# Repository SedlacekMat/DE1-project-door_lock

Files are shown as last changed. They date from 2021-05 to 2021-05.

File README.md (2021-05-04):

# Door lock with a four-digit PIN, twelve button keypad, a relay and the ability to change the PIN

### Team members

Sedláček David   
Sedláček Marek   
Sedláček Matyáš    
Sladkowski David     

[Github project folder]( https://github.com/SedlacekMat/DE1-project-door_lock)

### Project objectives

Create a door lock system with a PIN (4-digit) terminal, 12 push buttons, 4-digit 7-segment display and a relay for door lock control, with the ability to change the PIN after inputting the correct value. After not getting an input for a time, the device will reset itself.

Therefore we need to be able to: 
1. assign values to button presses, keep track of the position of the currently pressed digit
2. keep time for the autoreset after an idle period and for how long should the relay stay opened
3. store the value of the correct password in a way that enables changing it
4. compare the current value with the correct value for the current digit and eventually determine if the PIN is correct or not
5. drive a common anode 4-digit 7-segment display to show what has been pressed
6. make an external circuit for the buttons, relay, LEDs and display
7. make it work on Arty A7-35T/100T

## Hardware description
### ARTY A7-100

This project is based around the FPGA board ARTY A7-100T (has better capabilites when it comes to processing compared the ARTY A7-35T, therefore being better for potential future expansions, although if budget is a concern, the current version should run on the 35T as well with no problems). It is powered by 5V, the clock frequency is 100 MHz and has 256MB of RAM (DDR3L). Out of the available pins we have used the PMOD ones, which are grouped in four connectors of twelve pins (8 signal pins, 2 VCC, and 2 ground pins). Two of these connectors are high-speed, the other two are categorized as standard. The high-speed ones were used for the displays and the standard ones for buttons and such.

### External circuit

#### Schematic

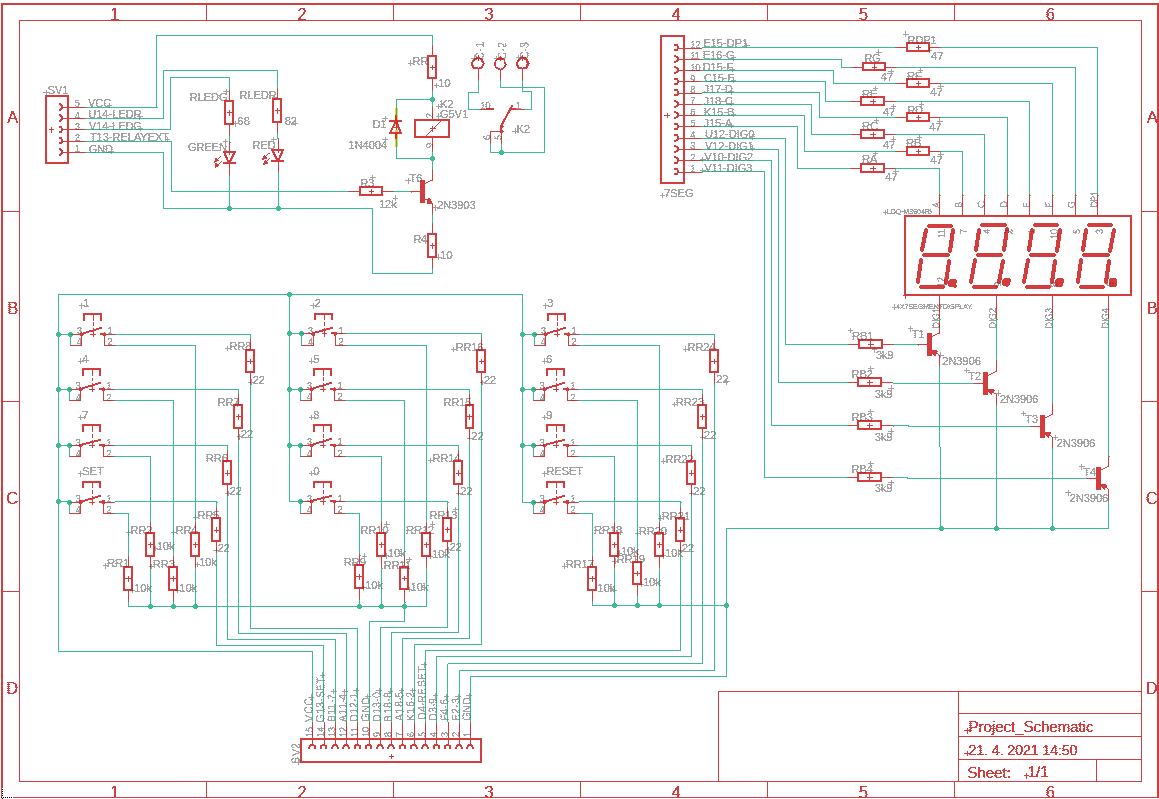
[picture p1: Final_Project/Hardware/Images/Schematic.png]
schematic


#### Used parts

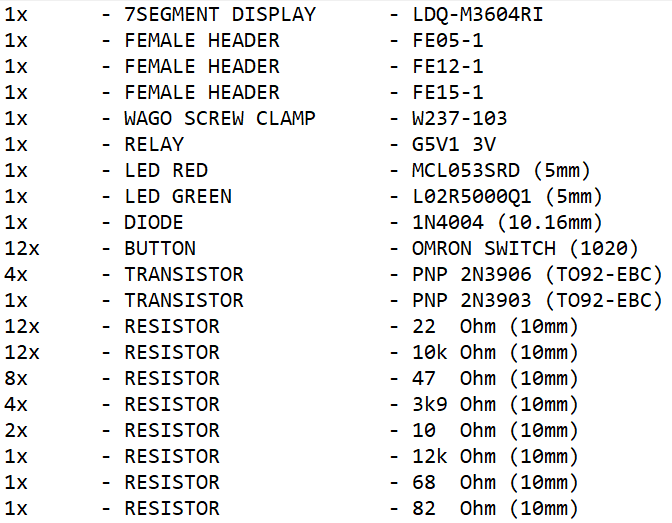
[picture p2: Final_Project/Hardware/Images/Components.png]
parts


#### Description

The external circuitry can be separated into three parts - the buttons, the display and the relay grouped with LEDs. 

The buttons have 3.3 V on their input, when a button is pressed, the voltage is transfered to the FPGA board input. They're connected to the supply voltage through 10k ohm resistors, this ensures that at the input of ARTY A7-100T, we can only get either a logical 1 or a logical 0, preventing undeterminable states. The 22 ohm resistors serve as protection. Each button has its own pin connection, due to the number of pins on the board being high enough for the projects needs. Potential improvement to save more pins (if the project were to be expanded input/output-wise) would be to connect them in a matrix.

For the display, the signals come in through 47 ohm resistors connected to the cathodes of the individual segments. The display used is the common anode type. The four PNP transistors are there to ensure only one display can be lit up at the same time. The anodes will be switching at periodic intervals, too fast for human vision, thus appearing as if all the diplays are lit at the same time.

As for the LEDs and the relay, the current through the red LED is limited by an 82 ohm resistor, 68 ohm for the green one. These prevent them from burning. The red LED will light up, if the PIN is incorrect, the green one in the opposite case. The relay is controlled by an NPN transistor, which, after it's base goes high, will open the relay. Connected parallel to the relay is a diode, through which the relay coil can discharge, after the relay is turned off.

Below are images of the PCB design

### PCB design

#### PCB top

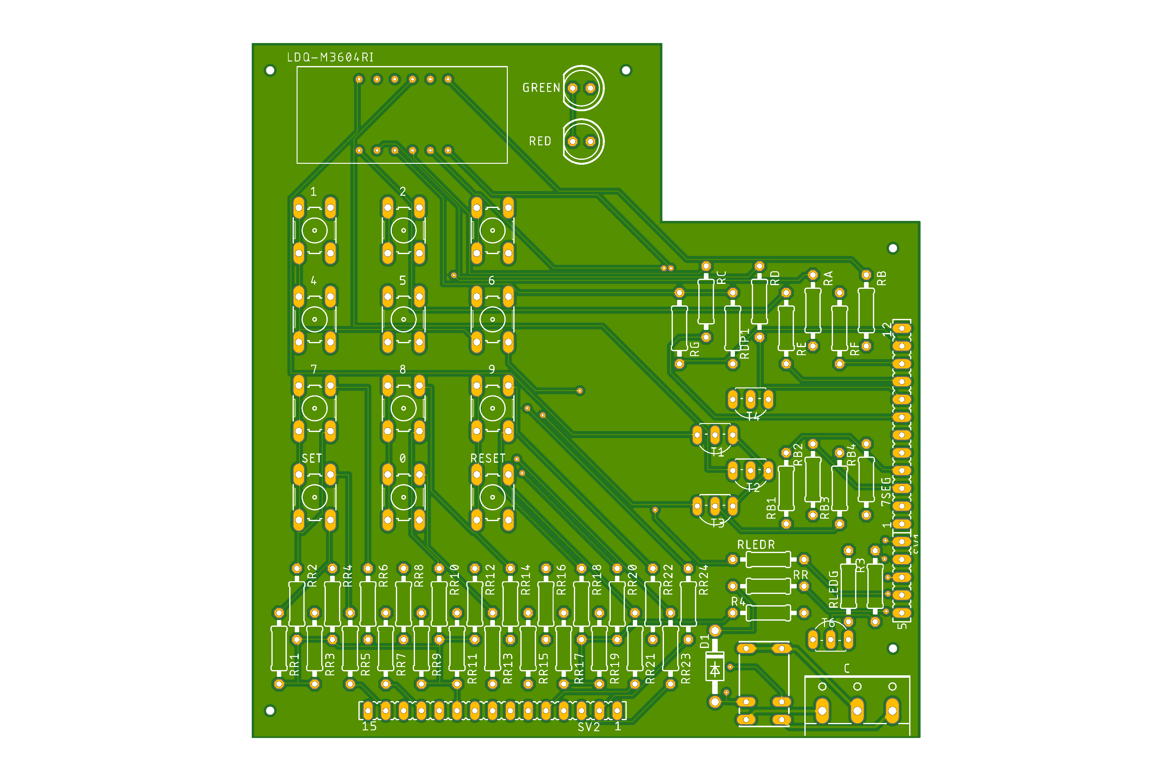
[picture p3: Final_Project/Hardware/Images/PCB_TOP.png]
PCBtop


#### PCB bottom

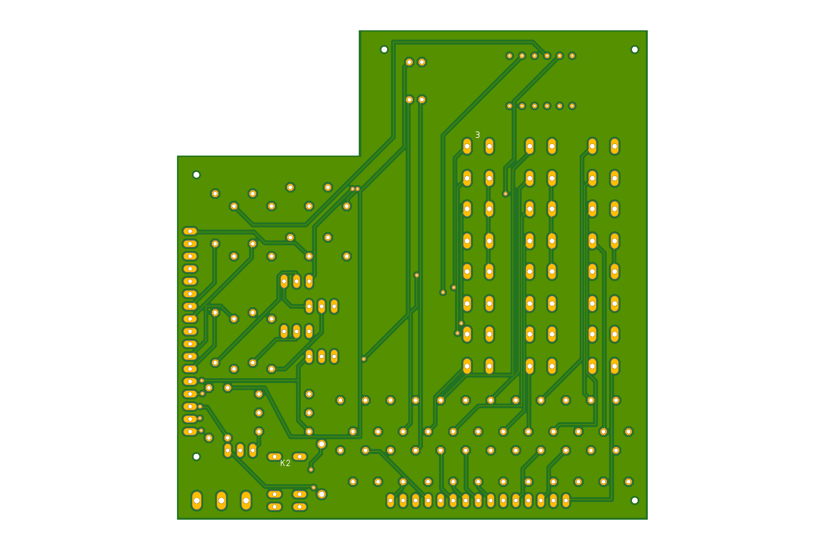
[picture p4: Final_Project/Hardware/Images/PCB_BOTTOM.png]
PCBbottom


#### PCB 3D model

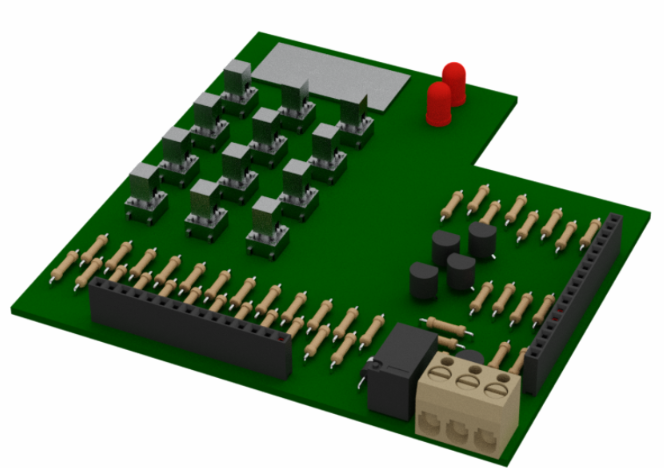
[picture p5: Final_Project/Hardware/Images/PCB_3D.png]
PCB3D


## VHDL modules description and simulations

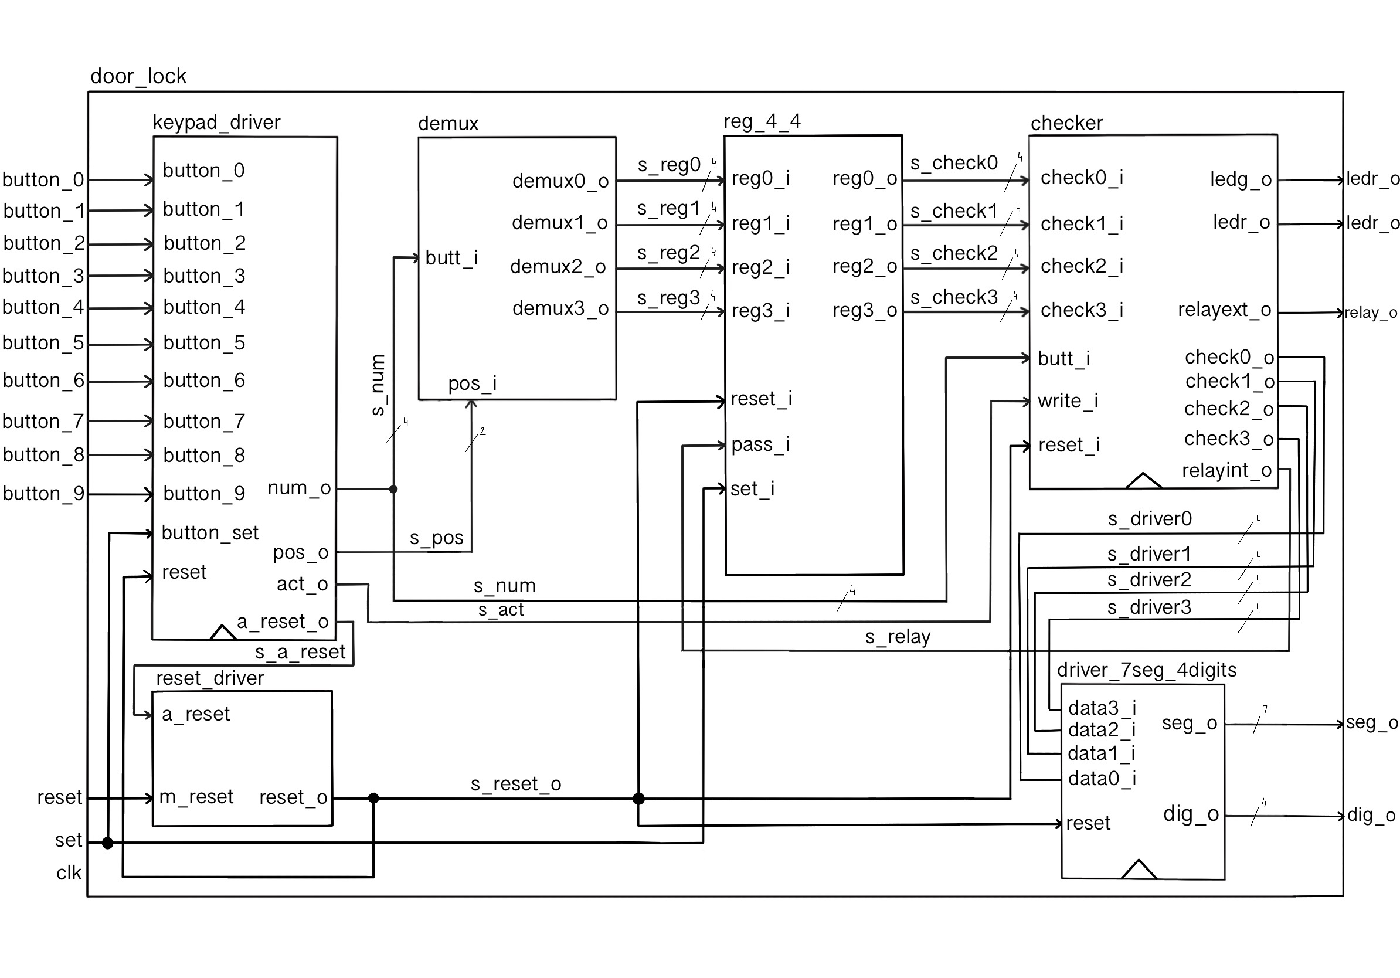
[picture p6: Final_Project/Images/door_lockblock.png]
doorlockblock


### keypad_driver

#### Visual representation:

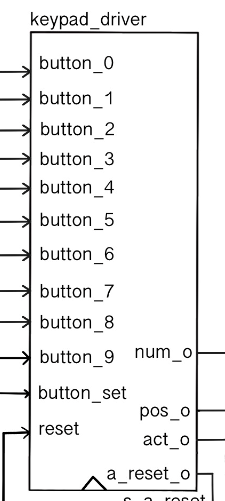
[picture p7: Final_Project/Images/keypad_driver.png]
keypaddriverblock


#### State diagram:

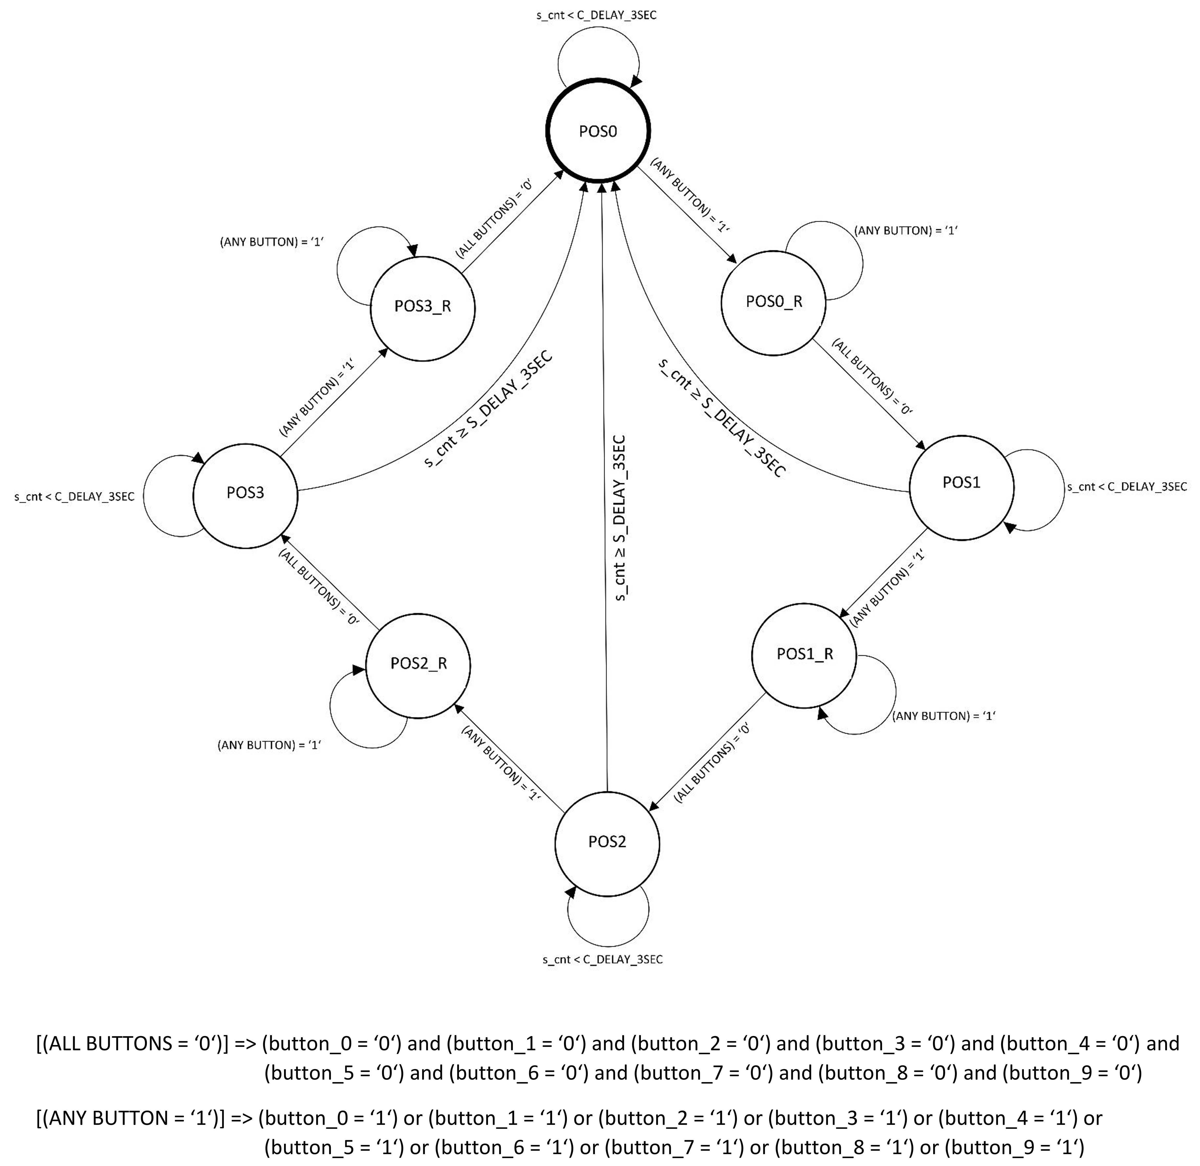
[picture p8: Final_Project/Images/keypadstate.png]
keypaddriverstate


#### Description:

The keypad_driver block functions as a middleman, first translating information from the input buttons and then transferring it to the checker block. A decision was made early in the project development to discard the idea of a button matrix input in favor of working with individual buttons, seeing as the FPGA board used has enough input/output pins to do so. This also determined parts of the design of the external board, which was shown and discussed above.

The keypad_driver provides the rest of the blocks with information about keypresses, assigns 4-bit values to buttons and keeps track of the position at which the value should appear. It uses a finite state machine to cycle through 4 positions using 8 states. The reason it uses 2 states (wait for press and wait for release) for each position, is to precisely determine whether the pressed button has been released, so it can without any doubt jump to the next position. While no button is pressed, the keypad-driver sends out a 4-bit signal of “1111”, indicating to the other blocks that there is no input.

Keypad_driver also handles the automatic reset function which activates after an idle period with no input. This function has been implemented so that the lock wipes itself in the case that someone inputs, for example, two values and walks off.

From the simulation waveforms, we see that the outputted position starts correctly indexing from 0, and (although we can't see here if they are actually correct, will be seen in the other simulations) button presses change the button value output's value. We can see that two buttons at the same time are sent out as only a single number out of the two (we can count button presses by s_act, only when it's '1' is the button press legitimate), which is important for the correct function of the rest of the blocks. We also see the autoreset turning on after an idle period with no button presses, here it's arbitrary, for the simulation to be fast, the time can be changed by changing the c_DELAY_1SEC to a more realistic value.

#### Simulation waveforms:

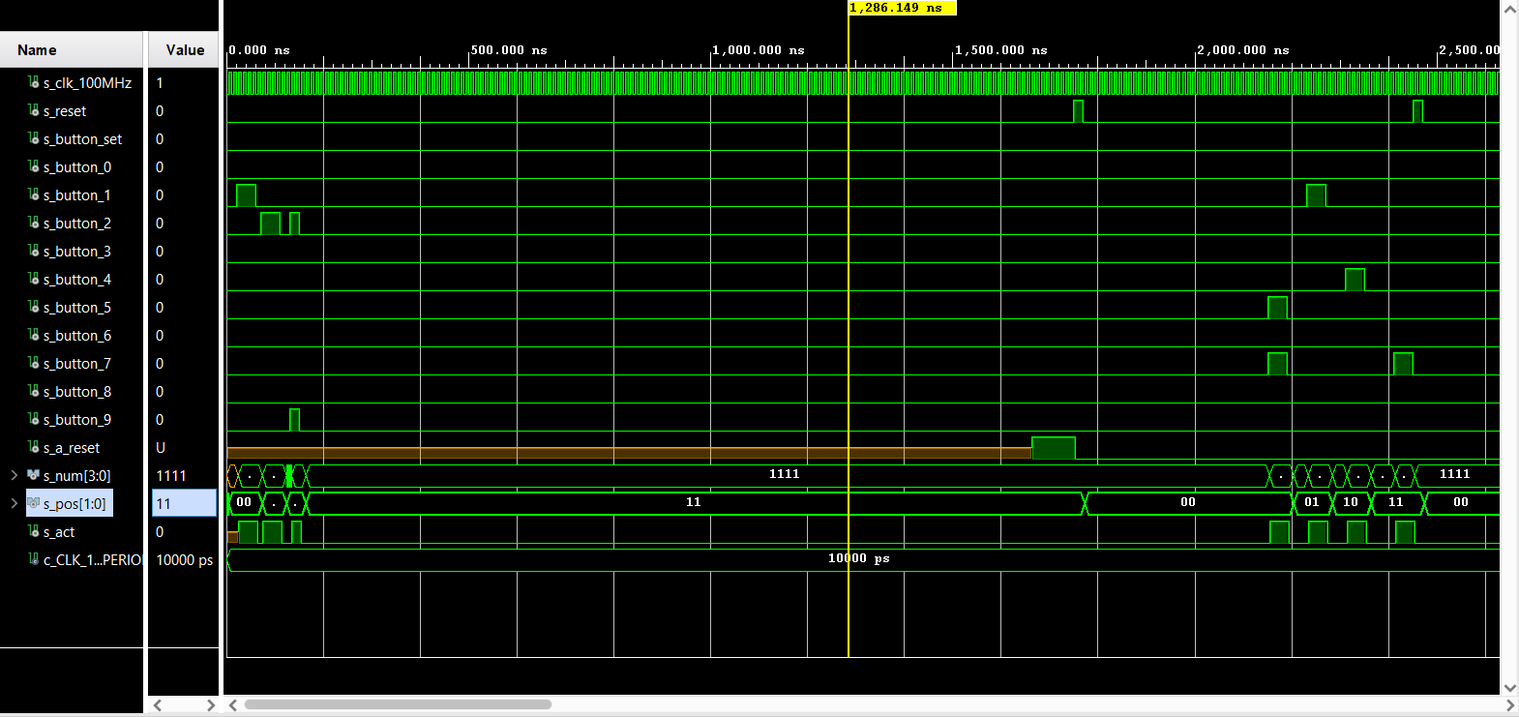
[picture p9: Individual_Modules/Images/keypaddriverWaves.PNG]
keypaddriverWaves


#### testbench: [tb_keypad_driver.vhd](Individual_Modules/Testbenches/tb_keypad_driver.vhd)

#### VHDL architecture:
```vhdl
architecture Behavioral of keypad_driver is

    type decoder_state is (POS0, POS0_R, POS1, POS1_R, POS2, POS2_R, POS3, POS3_R);
    signal s_state  : decoder_state;

    signal s_cnt    : unsigned(8 - 1 downto 0);

    constant c_DELAY_1SEC : unsigned(8 - 1 downto 0) := b"1001_0110";
    constant c_ZERO       : unsigned(8 - 1 downto 0) := b"0000_0000";
    
begin
    p_decoder_fsm : process(clk)
    begin
        if rising_edge(clk) then
            if (reset = '1') then
                s_state <= POS0;
                
                num_o   <= "1111";
                act_o   <= '0';
                -- Reset counter
                s_cnt   <= c_ZERO;
                
                a_reset_o <= '0';
           
            else
                case s_state is
                
                    when POS0 =>
                        
                        pos_o <= "00";
                        
                        if (button_0 = '1') then                          
                            num_o   <= "0000";
                            s_state <= POS0_R;
                            act_o <= '1';
                            s_cnt <= c_ZERO;
                        elsif (button_1 = '1') then   
                            num_o <= "0001";
                            s_state <= POS0_R;
                            act_o <= '1';
                            s_cnt <= c_ZERO;
                        elsif (button_2 = '1') then   
                            num_o <= "0010";
                            s_state <= POS0_R;
                            act_o <= '1';
                            s_cnt <= c_ZERO;
                        elsif (button_3 = '1') then   
                            num_o <= "0011";
                            s_state <= POS0_R;
                            act_o <= '1';
                            s_cnt <= c_ZERO;    
                        elsif (button_4 = '1') then   
                            num_o <= "0100";
                            s_state <= POS0_R;
                            act_o <= '1';
                            s_cnt <= c_ZERO;        
                        elsif (button_5 = '1') then   
                            num_o <= "0101";
                            s_state <= POS0_R;
                            act_o <= '1';
                            s_cnt <= c_ZERO;       
                        elsif (button_6 = '1') then   
                            num_o <= "0110";
                            s_state <= POS0_R;
                            act_o <= '1';
                            s_cnt <= c_ZERO;         
                        elsif (button_7 = '1') then   
                            num_o <= "0111";
                            s_state <= POS0_R;
                            act_o <= '1';
                            s_cnt <= c_ZERO;         
                        elsif (button_8 = '1') then   
                            num_o <= "1000";
                            s_state <= POS0_R;
                            act_o <= '1';
                            s_cnt <= c_ZERO;         
                        elsif (button_9 = '1') then   
                            num_o <= "1001";
                            s_state <= POS0_R;
                            act_o <= '1';
                            s_cnt <= c_ZERO;         
                        --else
                 
                        end if;
                        
                    when POS0_R =>
                        
                        pos_o <= "00";
                        
                        if (button_0 = '0' and button_1 = '0' and
                            button_2 = '0' and button_3 = '0' and
                            button_4 = '0' and button_5 = '0' and
                            button_6 = '0' and button_7 = '0' and
                            button_8 = '0' and button_9 = '0') then
                            s_state <= POS1;
                            act_o <= '0';     
                        end if;
                        
                    when POS1 =>
                        
                        pos_o <= "01";
                        
                        if (button_0 = '1') then                          
                            num_o   <= "0000";
                            s_state <= POS1_R;
                            act_o <= '1';
                            s_cnt <= c_ZERO;
                        elsif (button_1 = '1') then   
                            num_o <= "0001";
                            s_state <= POS1_R;
                            act_o <= '1';
                            s_cnt <= c_ZERO;   
                        elsif (button_2 = '1') then   
                            num_o <= "0010";
                            s_state <= POS1_R;
                            act_o <= '1';
                            s_cnt <= c_ZERO;        
                        elsif (button_3 = '1') then   
                            num_o <= "0011";
                            s_state <= POS1_R;
                            act_o <= '1';
                            s_cnt <= c_ZERO;
                        elsif (button_4 = '1') then   
                            num_o <= "0100";
                            s_state <= POS1_R;
                            act_o <= '1';
                            s_cnt <= c_ZERO;       
                        elsif (button_5 = '1') then   
                            num_o <= "0101";
                            s_state <= POS1_R;
                            act_o <= '1';
                            s_cnt <= c_ZERO;          
                        elsif (button_6 = '1') then   
                            num_o <= "0110";
                            s_state <= POS1_R;
                            act_o <= '1';
                            s_cnt <= c_ZERO;          
                        elsif (button_7 = '1') then   
                            num_o <= "0111";
                            s_state <= POS1_R;
                            act_o <= '1';
                            s_cnt <= c_ZERO;  
                        elsif (button_8 = '1') then   
                            num_o <= "1000";
                            s_state <= POS1_R;
                            act_o <= '1';
                            s_cnt <= c_ZERO;       
                        elsif (button_9 = '1') then   
                            num_o <= "1001";
                            s_state <= POS1_R;
                            act_o <= '1';
                            s_cnt <= c_ZERO;        
                        else
                            if (s_cnt < c_DELAY_1SEC) then
                                s_cnt <= s_cnt + 1;
                                num_o <= "1111";
                            else
                                -- s_state <= POS0;
                                -- s_cnt <= c_ZERO;
                                a_reset_o <= '1';
                            end if;  
                        end if;
                        
                    when POS1_R =>
                        
                        pos_o <= "01";
                        
                        if (button_0 = '0' and button_1 = '0' and
                            button_2 = '0' and button_3 = '0' and
                            button_4 = '0' and button_5 = '0' and
                            button_6 = '0' and button_7 = '0' and
                            button_8 = '0' and button_9 = '0') then
                            s_state <= POS2;
                            act_o <= '0';                        
                        end if; 
                       
                    when POS2 =>
                        
                        pos_o <= "10";
                        
                        if (button_0 = '1') then                          
                            num_o   <= "0000";
                            s_state <= POS2_R;
                            act_o <= '1';
                            s_cnt <= c_ZERO;
                        elsif (button_1 = '1') then   
                            num_o <= "0001";
                            s_state <= POS2_R;
                            act_o <= '1';
                            s_cnt <= c_ZERO; 
                        elsif (button_2 = '1') then   
                            num_o <= "0010";
                            s_state <= POS2_R;
                            act_o <= '1';
                            s_cnt <= c_ZERO;      
                        elsif (button_3 = '1') then   
                            num_o <= "0011";
                            s_state <= POS2_R;
                            act_o <= '1';
                            s_cnt <= c_ZERO;         
                        elsif (button_4 = '1') then   
                            num_o <= "0100";
                            s_state <= POS2_R;
                            act_o <= '1';
                            s_cnt <= c_ZERO;        
                        elsif (button_5 = '1') then   
                            num_o <= "0101";
                            s_state <= POS2_R;
                            act_o <= '1';
                            s_cnt <= c_ZERO;         
                        elsif (button_6 = '1') then   
                            num_o <= "0110";
                            s_state <= POS2_R;
                            act_o <= '1';
                            s_cnt <= c_ZERO;        
                        elsif (button_7 = '1') then   
                            num_o <= "0111";
                            s_state <= POS2_R;
                            act_o <= '1';
                            s_cnt <= c_ZERO;       
                        elsif (button_8 = '1') then   
                            num_o <= "1000";
                            s_state <= POS2_R;
                            act_o <= '1';
                            s_cnt <= c_ZERO;         
                        elsif (button_9 = '1') then   
                            num_o <= "1001";
                            s_state <= POS2_R;
                            act_o <= '1';
                            s_cnt <= c_ZERO;         
                        else
                            if (s_cnt < c_DELAY_1SEC) then
                                s_cnt <= s_cnt + 1;
                                num_o <= "1111";
                            else
                                -- s_state <= POS0;
                                -- s_cnt <= c_ZERO;
                                a_reset_o <= '1';
                            end if;                            
                        end if;
                        
                    when POS2_R =>
                        
                        pos_o <= "10";
                        
                        if (button_0 = '0' and button_1 = '0' and
                            button_2 = '0' and button_3 = '0' and
                            button_4 = '0' and button_5 = '0' and
                            button_6 = '0' and button_7 = '0' and
                            button_8 = '0' and button_9 = '0') then
                            s_state <= POS3;
                            act_o <= '0';                      
                        end if; 
                        
                    when POS3 =>
                        
                        pos_o <= "11";
                        
                        if (button_0 = '1') then                          
                            num_o   <= "0000";
                            s_state <= POS3_R;
                            act_o <= '1';
                            s_cnt <= c_ZERO;
                        elsif (button_1 = '1') then   
                            num_o <= "0001";
                            s_state <= POS3_R;
                            act_o <= '1';
                            s_cnt <= c_ZERO;    
                        elsif (button_2 = '1') then   
                            num_o <= "0010";
                            s_state <= POS3_R;
                            act_o <= '1';
                            s_cnt <= c_ZERO;         
                        elsif (button_3 = '1') then   
                            num_o <= "0011";
                            s_state <= POS3_R;
                            act_o <= '1';
                            s_cnt <= c_ZERO;         
                        elsif (button_4 = '1') then   
                            num_o <= "0100";
                            s_state <= POS3_R;
                            act_o <= '1';
                            s_cnt <= c_ZERO;        
                        elsif (button_5 = '1') then   
                            num_o <= "0101";
                            s_state <= POS3_R;
                            act_o <= '1';
                            s_cnt <= c_ZERO;        
                        elsif (button_6 = '1') then   
                            num_o <= "0110";
                            s_state <= POS3_R;
                            act_o <= '1';
                            s_cnt <= c_ZERO;        
                        elsif (button_7 = '1') then   
                            num_o <= "0111";
                            s_state <= POS3_R;
                            act_o <= '1';
                            s_cnt <= c_ZERO;       
                        elsif (button_8 = '1') then   
                            num_o <= "1000";
                            s_state <= POS3_R;
                            act_o <= '1';
                            s_cnt <= c_ZERO;         
                        elsif (button_9 = '1') then   
                            num_o <= "1001";
                            s_state <= POS3_R;
                            act_o <= '1';
                            s_cnt <= c_ZERO;
                        else
                            if (s_cnt < c_DELAY_1SEC) then
                                s_cnt <= s_cnt + 1;
                                num_o <= "1111";
                            else
                                -- s_state <= POS0;
                                -- s_cnt <= c_ZERO;
                                a_reset_o <= '1';
                            end if;
                        end if;
                        
                    when POS3_R =>
                        
                        pos_o <= "11";
                        
                        if (button_0 = '0' and button_1 = '0' and
                            button_2 = '0' and button_3 = '0' and
                            button_4 = '0' and button_5 = '0' and
                            button_6 = '0' and button_7 = '0' and
                            button_8 = '0' and button_9 = '0' and
                            button_set = '0') then
                            s_state <= POS0;
                            act_o <= '0';          
                        end if; 
                                   
                end case;
            end if; 
        end if;
    end process p_decoder_fsm; 

end Behavioral;
``` 

### reset_driver

#### Visual representation:

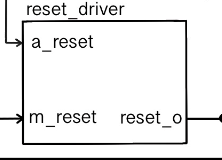
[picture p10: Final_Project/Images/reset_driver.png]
resetdriverblock


#### Description:

Reset driver is a simple block, working as an OR gate for 2 input signals. Both are one-bit signals, one sent form keypad_driver as an auto-reset, the other is connected to the reset button on the external board. After any of reset_driver’s inputs is set HIGH (equal to ‘1’) it drives the output signal HIGH as well, which in this case resets all the modules connected to the output. It has been created to enable the keypad_driver to reset the whole project.

#### Simulation waveforms:

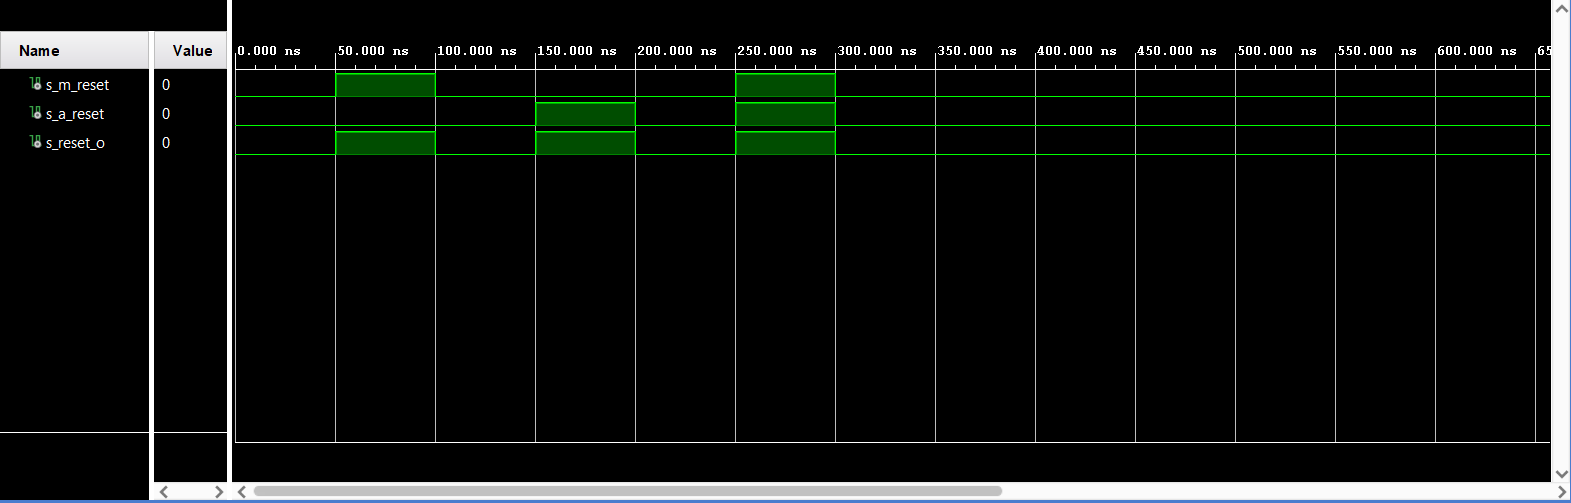
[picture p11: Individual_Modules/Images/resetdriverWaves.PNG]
resetdriverWaves


#### testbench: [tb_reset_driver.vhd](Individual_Modules/Testbenches/tb_reset_driver.vhd)

#### VHDL architecture:
```vhdl
architecture Behavioral of reset_driver is

begin
    p_reset_driver : process(m_reset, a_reset)
    begin
        
        if (a_reset = '1' or m_reset = '1') then
            reset_o <= '1';
        else
            reset_o <= '0';
        end if;
        
    end process p_reset_driver;

end Behavioral;
``` 

### demux

#### Visual representation:

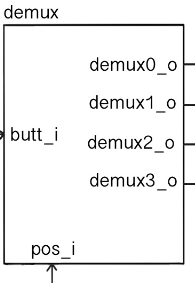
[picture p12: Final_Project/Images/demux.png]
demuxblock


#### Description:

This block is, as the name suggests, a demultiplexer. It's job is to assign the 4-bit button value input (butt_i) to one of the outputs based on the value of the 2-bit position input (pos_i). It's the first block of the two block system for the storage of the correct combination. It is always active, even when the PIN is not being changed, since there is no need to turn it off, that becomes important only on the second block of the password storage system, the 4 times 4-bit register.

In the simulation we see the behaviour exactly as described above, the input being assigned to an output based on the value of the position coming in from keypad_driver.

#### Simulation waveforms:

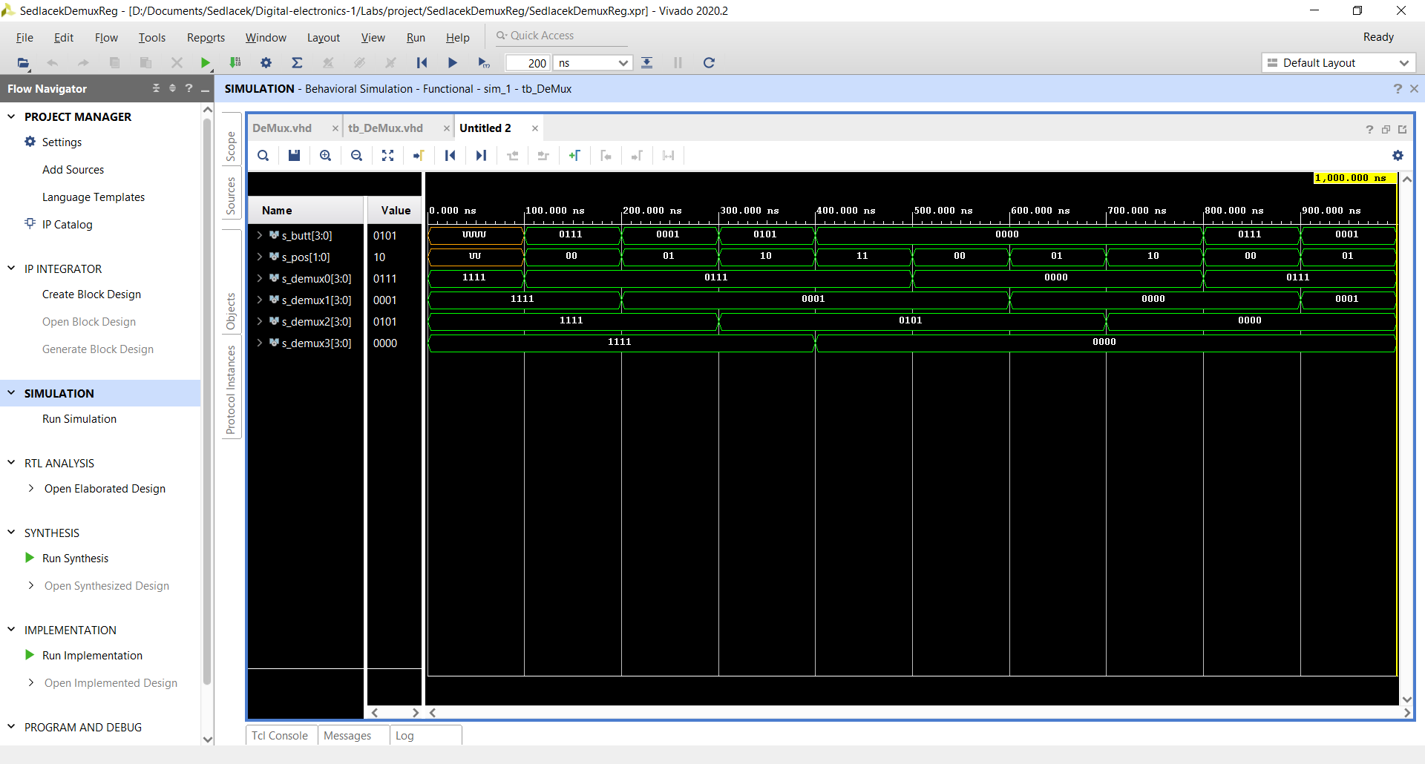
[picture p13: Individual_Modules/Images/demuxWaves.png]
demuxWaves


#### testbench: [tb_DeMux.vhd](Individual_Modules/Testbenches/tb_DeMux.vhd)

#### VHDL architecture:
```vhdl
architecture Behavioral of demux is
        begin
        
        p_demux : process(pos_i, butt_i)
        begin

            case pos_i is
                when "00" => 
                    demux0_o <= butt_i;
                when "01" => 
                    demux1_o <= butt_i;
                when "10" => 
                    demux2_o <= butt_i;
                when "11" => 
                    demux3_o <= butt_i;
                when others =>
                    demux0_o <= "1111";
                    demux1_o <= "1111";
                    demux2_o <= "1111";
                    demux3_o <= "1111";
             end case;      
        
        end process p_demux;
    end Behavioral;
``` 

### reg_4_4

#### Visual representation:

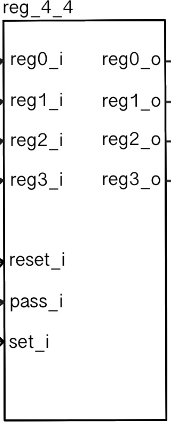
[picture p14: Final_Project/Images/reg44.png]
reg44block


#### Description:

This block is a 16-bit register, split into four 4-bit registers. In principle, it's basically a group of D latches with a condition on the enable input. It's job is to, if the set_i (activated by a button which must be held) and pass_i (which is active ONLY when the door is unlocked by entering the correct password, for a predetermined amount of time) inputs are set high, record and store the inputs coming from the demultiplexer into the correct outputs, thus changing the combination of values that the checker block (where the comparation of the current and correct values takes place) will read. In the situation that the set_i, pass_i and reset_i inputs are all activated, the correct PIN (register output) will change to the combination "3142". The local check signal is present so that the register isn't permanently stuck in the default password branch.

In the simulation waves, we see that just the pass_i has no effect. When combined with set_i, input values start getting assigned to their corresponding output. If only set is on, nothing changes, (same for reset, not shown here, but obvious from the final project waveforms). If pass,set and reset are on, we change to the default combination.

#### Simulation waveforms:

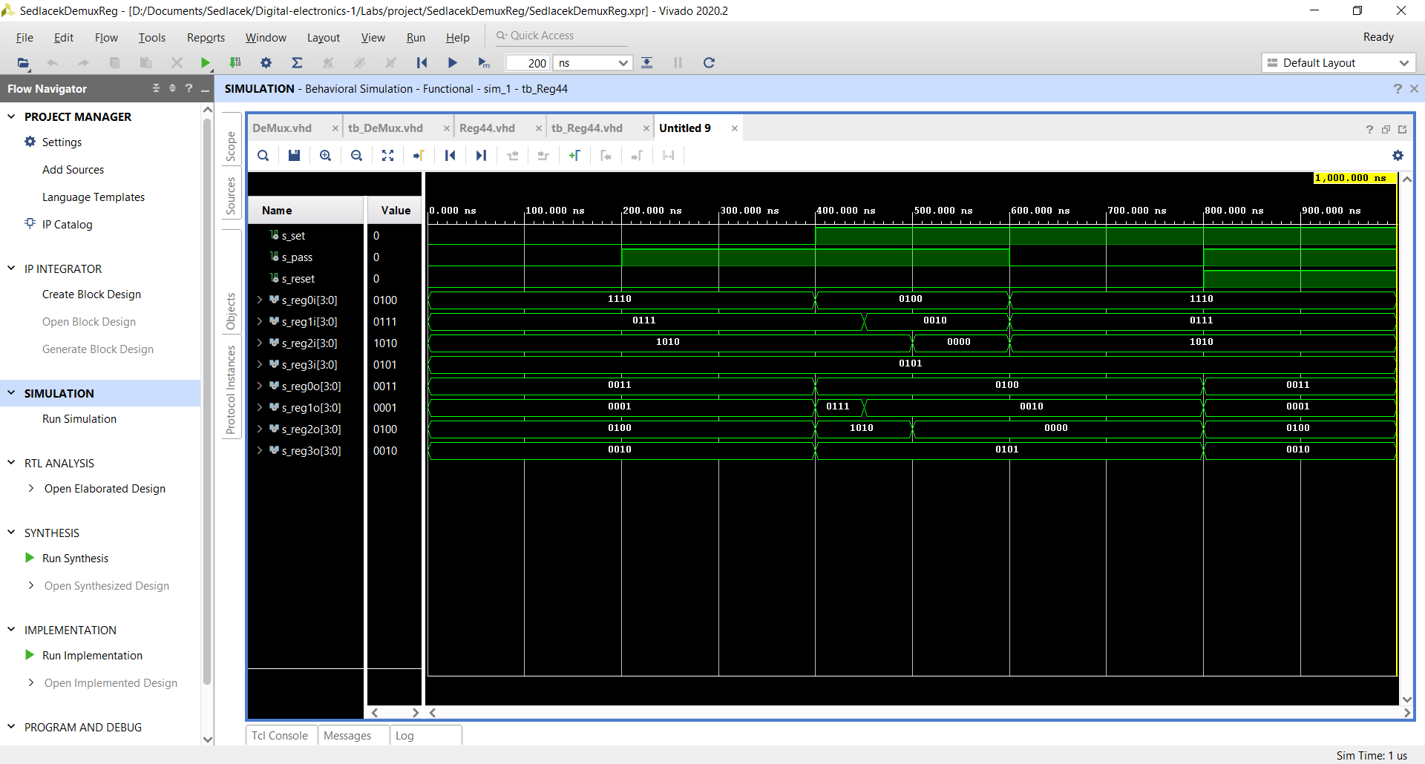
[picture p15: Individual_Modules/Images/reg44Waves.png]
reg44Waves


#### testbench: [tb_Reg44.vhd](Individual_Modules/Testbenches/tb_Reg44.vhd)

#### VHDL architecture:
```vhdl

architecture Behavioral of reg_4_4 is

    signal s_local_check : std_logic;

begin

    p_register : process(pass_i, set_i, reset_i, reg0_i, reg1_i, reg2_i, reg3_i)
    begin
    
    if (pass_i='1' and set_i='1' and reset_i='1') then
            reg0_o <= "0011";
            reg1_o <= "0001";
            reg2_o <= "0100";
            reg3_o <= "0010";
            s_local_check <= '1';
    elsif (pass_i='1' and set_i='1' and reset_i='0' and s_local_check <= '0') then
            reg0_o <= reg0_i;
            reg1_o <= reg1_i;
            reg2_o <= reg2_i;
            reg3_o <= reg3_i;
    elsif (set_i = '0') then -- pass_i='1' and
        s_local_check <= '0';
    end if;
    
    end process p_register;
end Behavioral;
``` 

### checker

#### Visual representation:

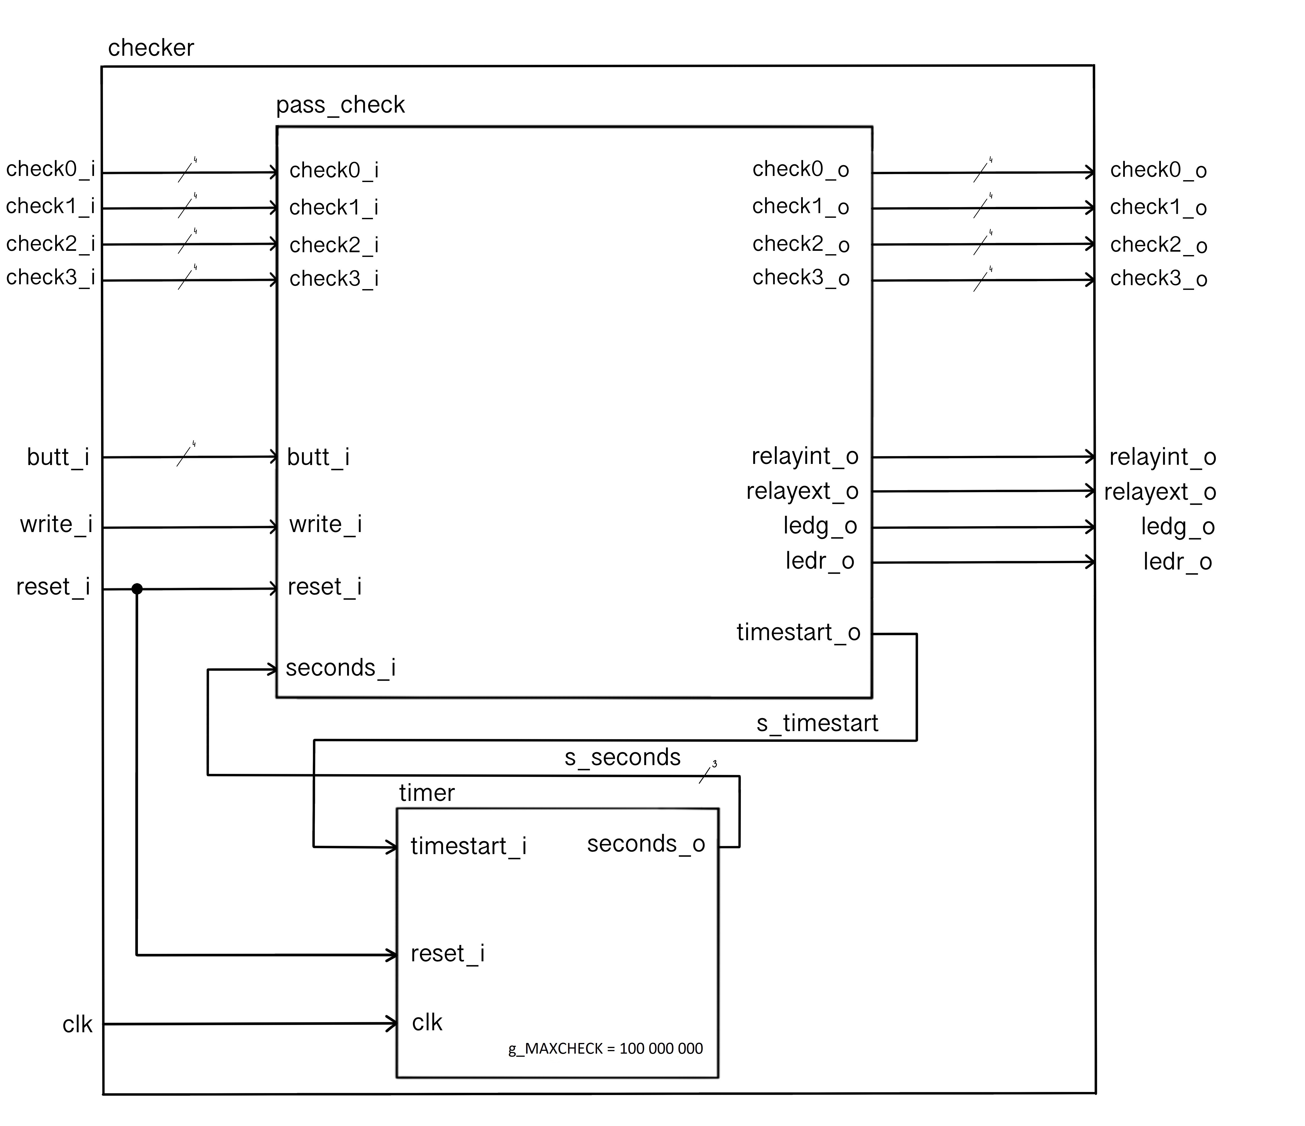
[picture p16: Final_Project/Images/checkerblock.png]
checkerblock


#### Description:

The checker block is an amalgamation of two separate blocks, pass_check (the Moore FSM for judging the entered combination) and the timer block.

The simulation waveform will be described for each block separately, the screenshot below can be referred to later for verification.

#### Simulation waveforms:

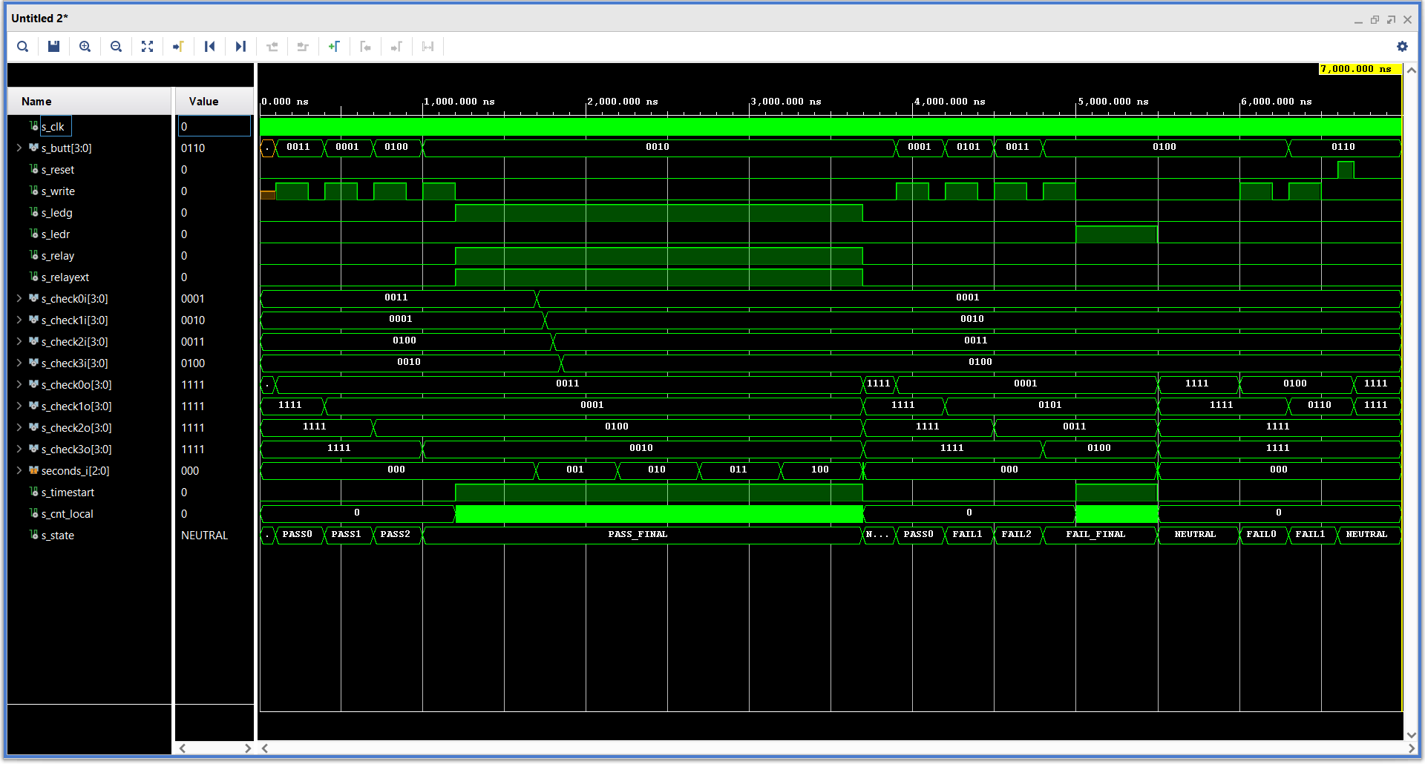
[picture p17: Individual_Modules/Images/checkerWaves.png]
checkerWaves


#### testbench: [tb_checker.vhd](Individual_Modules/Testbenches/tb_checker.vhd)

#### VHDL architecture:
```vhdl
architecture Behavioral of checker is

    signal s_timestart  : std_logic;
    signal s_seconds    : std_logic_vector(2 downto 0);

begin

    timer0 : entity work.timer
    
        generic map(
            g_MAXCHECK => 50 -- realistically 100 000 000
        )
        port map(
            clk => clk,
            reset_i => reset_i,
            timestart_i => s_timestart,
            seconds_o => s_seconds 
        );
        
    pass_check0 :  entity work.pass_check
          port map(
                butt_i       =>  butt_i,
                reset_i      =>  reset_i,
                write_i      =>  write_i,
                seconds_i    =>  s_seconds,
                ledg_o       =>  ledg_o,
                ledr_o       =>  ledr_o,
                relayint_o   =>  relayint_o,
                relayext_o   =>  relayext_o,
                timestart_o  =>  s_timestart,
                check0_i     =>  check0_i,
                check1_i     =>  check1_i,
                check2_i     =>  check2_i,
                check3_i     =>  check3_i,
                check0_o     =>  check0_o,
                check1_o     =>  check1_o,
                check2_o     =>  check2_o,
                check3_o     =>  check3_o
                                
                );  

end Behavioral;
``` 

### pass_check

#### State diagram:

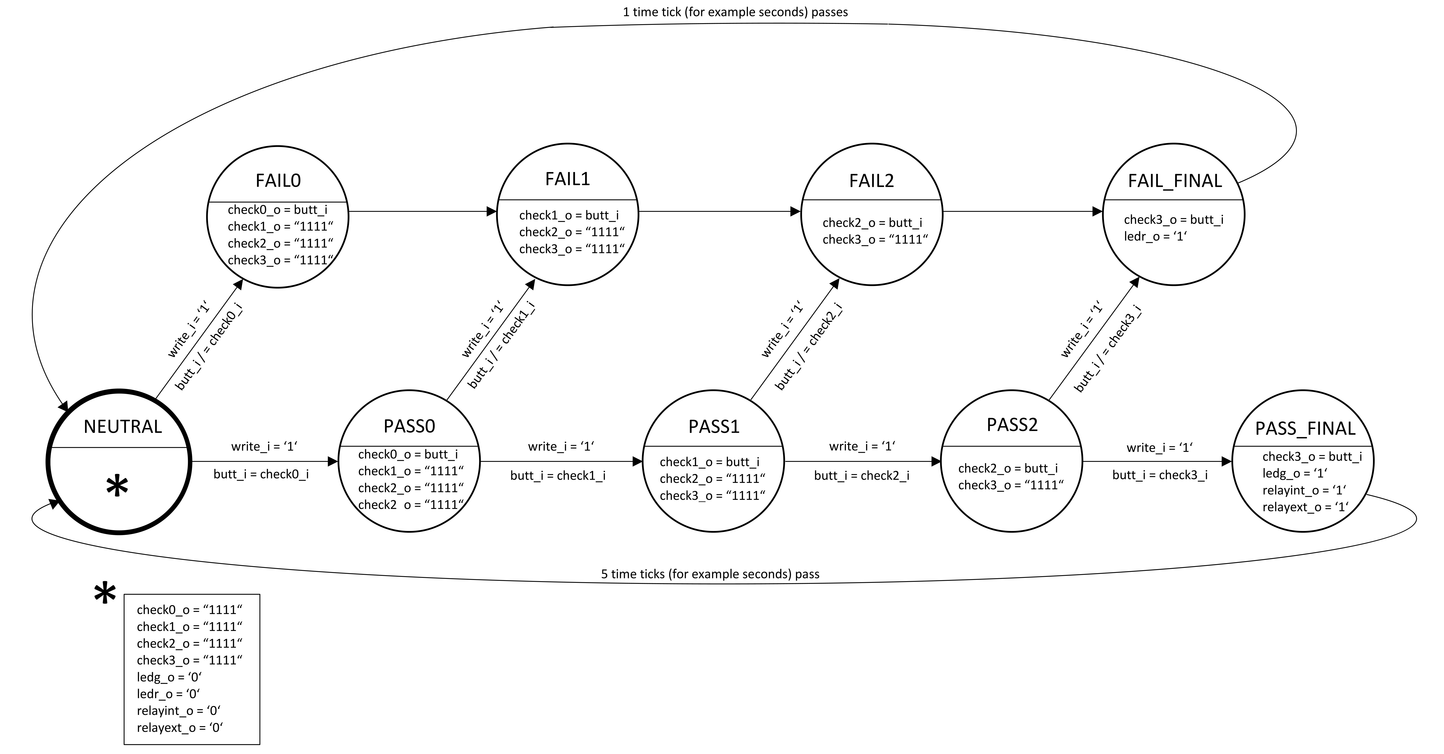
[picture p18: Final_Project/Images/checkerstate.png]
passcheckstate


#### Description:

As stated, this is a Moore type finite state machine, meaning that the outputs are determined by the current state. As we can see from the diagram, we have an initial NEUTRAL state, where all the outputs are off and the combination being sent to the displays is "1111", which the diplay driver interprets as "nothing lights up". When a button is pressed, it's value comes through the butt_i input and the write_i input activates, that way, we ensure we process only legitimate button presses and enables us to read the same value pressed twice as two separate inputs.

When we detect a legitimate button press, we compare the value at butt_i to the value of the passwords first number (check0_i), if they match, the state changes to PASS0, if they don't, we go to FAIL0 and so on. This means, each button press is compared separately. Two things to note are: Firstly, that we can slip into a fail state at each separate button press and not know about it until we enter the whole combination. All inputs are outputted to the display no matter if they are correct or not. Secondly, if the reset_i is activated at any time (either manually or automatically by keypad_driver), we are returned back to the NEUTRAL state. This is NOT incorporated into the state diagram, since it quickly becomes overcrowded by lines and conditions and results mostly in confusion, which defeats the purpose of making a state diagram in the first place.

We see the diagram has two branches, at the end of each there is a final state, either FAIL_FINAL or PASS_FINAL. FAIL_FINAL results in the red LED turning on and it sends a signal through the timestart_o output to the timer, which starts counting one "tick" of time (in the real implementation seconds, had to be shortened in the simulation). When the correct number of ticks is read on the seconds_i input, the state shifts to the NEUTRAL state. Similarly to this the PASS_FINAL state activates the green LED and opens the relay for five time "ticks" (time is kept by the same mechanism as above). During this, it also send an internal signal through the relayint_o output to the reg_4_4 register, which allows the user to change the correct combination for the duration of these five "ticks". After those pass, pass_check shifts to the NEUTRAL state. If we change the combination to the default one by pressing set and reset, it shifts to NEUTRAL immediately.

There is potential for future improvement here, namely that the relayint_o could stay on indefinetly, as long as set is pressed during the time that relayint_o was 
already turned on by the door opening.

From the simulation waveforms we see that the finite state machine is working as intended (described above), outputted values for the display are in the correct position, LEDs, relay and timestart turn on appropriately, and in NEUTRAL all outputs go to "1111". Note that the FINAL states are not timed since this is only the pass_check block.

#### Simulation waveforms:

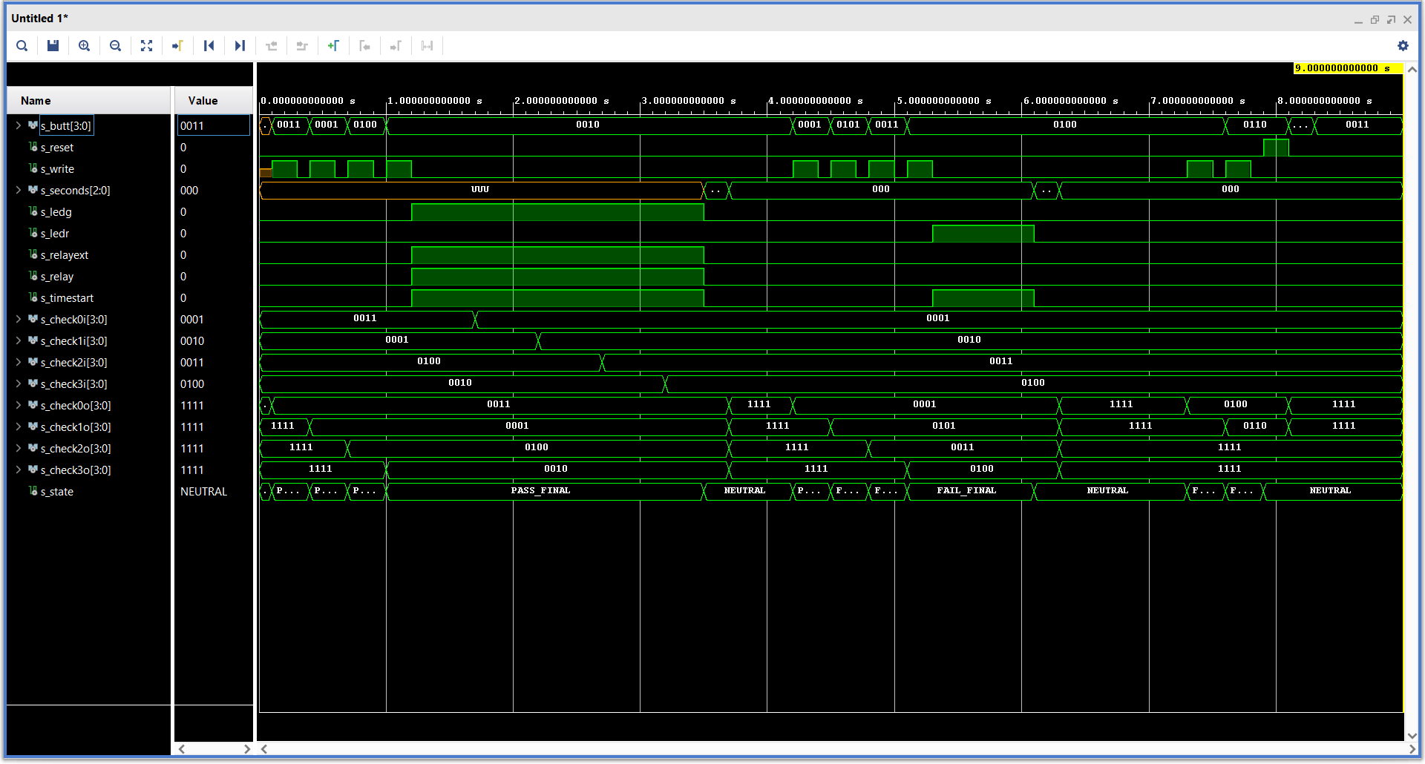
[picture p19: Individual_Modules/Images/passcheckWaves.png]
passcheckWaves


#### testbench: [tb_passCheck.vhd](Individual_Modules/Testbenches/tb_passCheck.vhd)

#### VHDL architecture:
```vhdl
architecture Behavioral of pass_check is
    type t_state is (NEUTRAL,
                     PASS0,
                     PASS1,
                     PASS2,
                     PASS_FINAL,
                     FAIL0,
                     FAIL1,
                     FAIL2,
                     FAIL_FINAL);
    
    signal s_state  : t_state;

begin
    
    p_passcheck: process(reset_i, write_i, butt_i,seconds_i, check0_i, check1_i, check2_i, check3_i)
    begin
        if (reset_i ='1') then
            s_state <= NEUTRAL;
        elsif (reset_i ='0') then
            case s_state is 
                
                when NEUTRAL =>
                
                    timestart_o <= '0';
                    ledg_o <= '0';
                    ledr_o <= '0';
                    relayint_o <= '0';
                    relayext_o <= '0';
                
                    check0_o <= "1111";
                    check1_o <= "1111";
                    check2_o <= "1111";
                    check3_o <= "1111";
                    if ((check0_i = butt_i) and write_i = '1') then
                        check0_o <= butt_i;
                        s_state <= PASS0;
                    elsif ((check0_i /= butt_i) and write_i = '1') then
                        check0_o <= butt_i;
                        s_state <= FAIL0;
                    else
                        null;
                    end if;
                    
                when PASS0 =>
                    if ((check1_i = butt_i) and write_i = '1') then
                        check1_o <= butt_i;
                        s_state <= PASS1;
                    elsif ((check1_i /= butt_i) and write_i = '1') then
                        check1_o <= butt_i;
                        s_state <= FAIL1;
                    else
                        null;
                    end if;
                
                when PASS1 =>
                    if ((check2_i = butt_i) and write_i = '1') then
                        check2_o <= butt_i;
                        s_state <= PASS2;
                    elsif ((check2_i /= butt_i) and write_i = '1') then
                        check2_o <= butt_i;
                        s_state <= FAIL2;
                    else
                        null;
                    end if;
                
                when PASS2 =>
                    if ((check3_i = butt_i) and write_i = '1') then
                        check3_o <= butt_i;
                        s_state <= PASS_FINAL;
                    elsif ((check3_i /= butt_i) and write_i = '1') then
                        check3_o <= butt_i;
                        s_state <= FAIL_FINAL;
                    else
                        null;
                    end if;
                    
                when PASS_FINAL =>
                    timestart_o <= '1';
                    if (seconds_i < "101") then
                        ledg_o <= '1';
                        relayint_o <= '1';
                        relayext_o <= '1';
                    elsif (seconds_i = "101") then
                        ledg_o <= '0';
                        relayint_o <= '0';    
                        relayext_o <= '0';                       
                        timestart_o <= '0';
                        s_state <= NEUTRAL;
                    end if;
                
                when FAIL0 =>
                    if (write_i = '1') then
                        check1_o <= butt_i;
                        s_state <= FAIL1;
                    end if;    
                
                when FAIL1 =>
                    if (write_i = '1') then
                        check2_o <= butt_i;
                        s_state <= FAIL2;
                    end if;
                    
                when FAIL2 =>
                    if (write_i = '1') then
                        check3_o <= butt_i;
                        s_state <= FAIL_FINAL;
                    end if;
                
                when FAIL_FINAL =>
                    timestart_o <= '1';
                    if (seconds_i < "001") then
                        ledr_o <= '1';
                        relayint_o <= '0'; 
                        relayext_o <= '0'; 
                    elsif (seconds_i = "001") then
                        ledr_o <= '0';                        
                        timestart_o <= '0';
                        s_state <= NEUTRAL;
                    end if;
                    
                when others =>
                    s_state <= NEUTRAL;
                    
              end case;
             end if;
           end process p_passcheck;     
                  
end Behavioral;
``` 

### timer

#### Description:

As soon as timestart_i activates, this block starts counting clock pulses. There are two counters, one is, as mentioned, for individual clock pulses, the other is for counting how many times has the previous counter filled (determined by a constant), thus counting the time "ticks" that have passed. The second counter is outputted to seconds_o, which is read by pass_check, once it reads the correct number from its seconds_i, it shifts to NEUTRAL, in which, timestart_o is deactivated. This effectively resets the timer and it stops counting clock pulses.

In the simulation waveforms, we see that once timestart activates, we start counting clock periods locally, and each set number of periods, the seconds output changes its values up by one until the timestart input goes to zero. Here we count higher than 101 since nothing is stopping the timer, because timestart is controlled by pass_check.

#### Simulation waveforms:

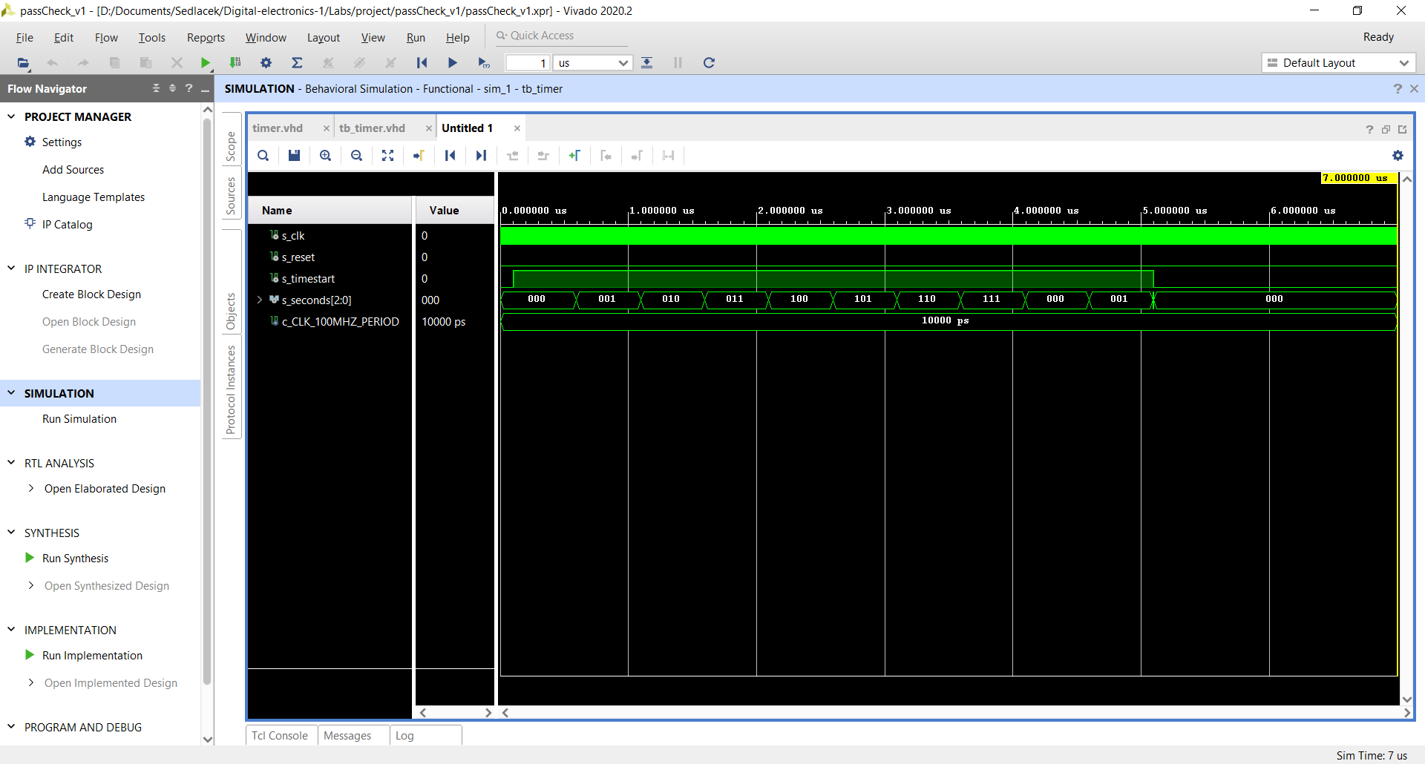
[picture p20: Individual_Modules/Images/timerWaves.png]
timerWaves


#### testbench: [tb_timer.vhd](Individual_Modules/Testbenches/tb_timer.vhd)

#### VHDL architecture:
```vhdl
architecture Behavioral of timer is
        signal s_cnt_local : natural:= 0;
        signal s_seconds_local : natural:= 1;
begin

p_timer: process(clk)
      begin 
        if timestart_i = '1' then
          if rising_edge(clk) then
              if  (reset_i = '1') then
                    s_cnt_local <= 0;
                    seconds_o <= "000";
              elsif (s_cnt_local >= (g_MAXCHECK - 1)) then
                  s_cnt_local <= 0;                
                  s_seconds_local <= (s_seconds_local + 1);
                  seconds_o <= std_logic_vector(TO_UNSIGNED(s_seconds_local,3)); 
              else
                  s_cnt_local <= (s_cnt_local + 1);
              end if;
          end if;
          elsif timestart_i = '0' then
          seconds_o <= "000"; 
          s_seconds_local <= 1;
          s_cnt_local <= 0;
        end if;
                           
      end process p_timer;  

end Behavioral;
``` 

### driver_7seg_4digits

#### Visual representation:

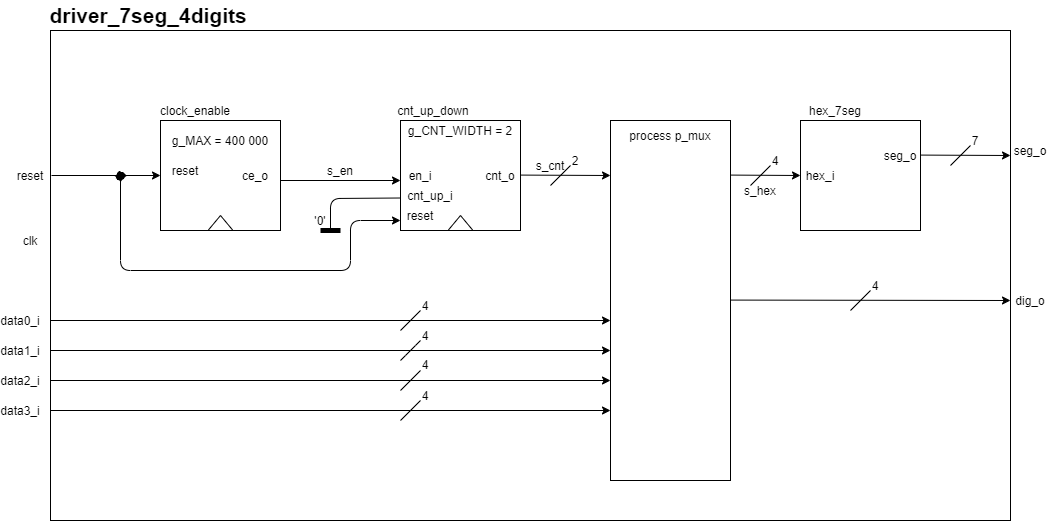
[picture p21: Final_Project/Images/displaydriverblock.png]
displaydriverblock


#### Description:

This block and its parts serve, as the name implies, as a driver for the four digit seven segment display used to display the typed in combination, receiving the outputs from the checker block. It was almost entirely pre-made (created during the semester in computer excersises) and only very slightly modified for the specific needs of this project, in the case of hex7seg and the p_mux process. The two main functions of the driver are: one, it connects all the sub-blocks together, two, it hosts the multiplexer process, that is needed to drive multi-digit seven segment displays, switching between the displays at a constant interval, too fast for human perception (here it's 4ms per display, shortened for simulation). The output for the decimal point was removed after some deliberation, originally there was an idea to use the decimal point as an indicator that the wrong combination has been entered, but it was foregone in the favor of having an external LED serve this purpose, driven by the checker block. 

From the simulation waveforms, we can see that the input numbers are being diplayed correctly and the anode is being changed in the desired order, so that the displays show the values from left to right.

#### Simulation waveforms:

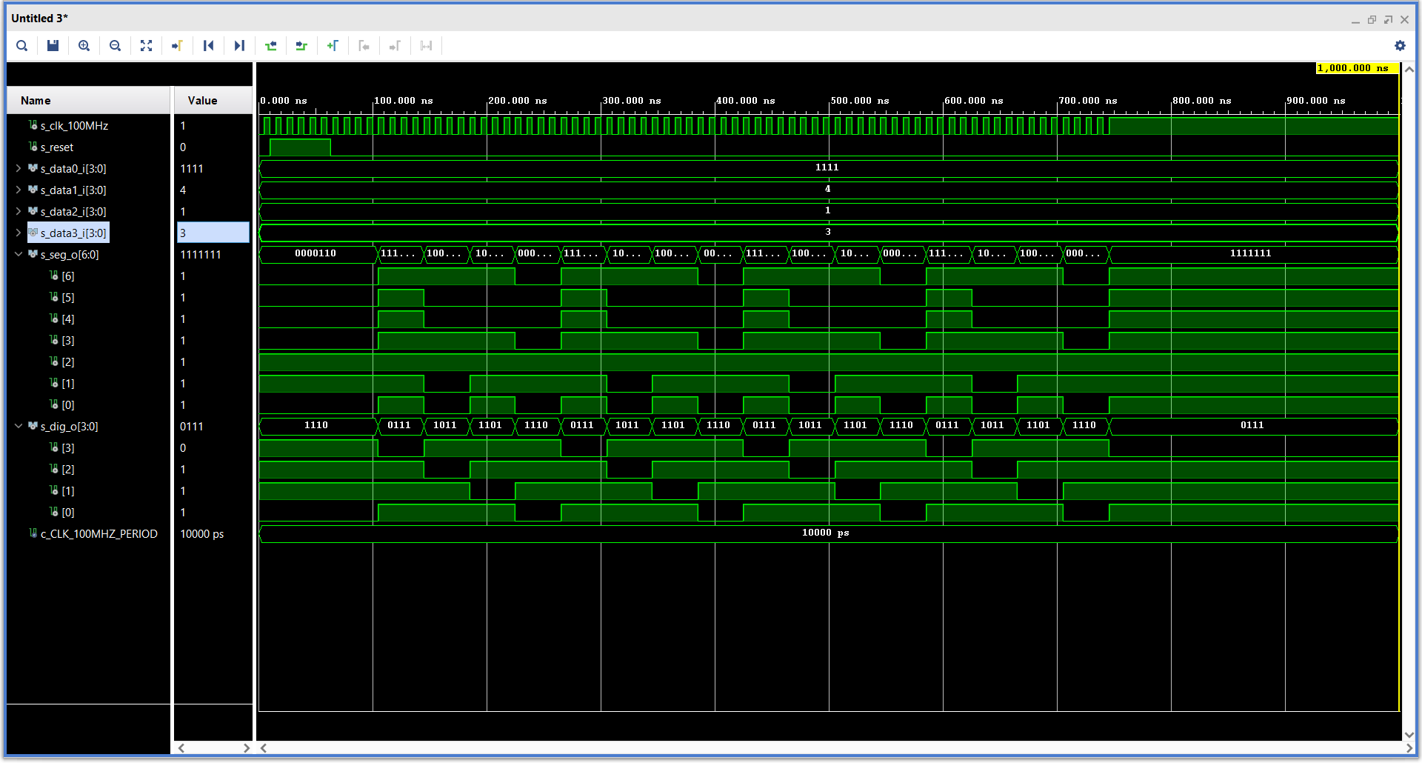
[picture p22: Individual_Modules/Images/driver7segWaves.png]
displaydriverWaves


#### testbench: [tb_driver_7seg_4digits.vhd](Individual_Modules/Testbenches/tb_driver_7seg_4digits.vhd)

#### VHDL architecture:
```vhdl
architecture Behavioral of driver_7seg_4digits is

    -- Internal clock enable
    signal s_en  : std_logic;
    -- Internal 2-bit counter for multiplexing 4 digits
    signal s_cnt : std_logic_vector(2 - 1 downto 0);
    -- Internal 4-bit value for 7-segment decoder
    signal s_hex : std_logic_vector(4 - 1 downto 0);

begin
    --------------------------------------------------------------------
    -- Instance (copy) of clock_enable entity generates an enable pulse
    -- every 4 ms
    clk_en0 : entity work.clock_enable
        generic map(
            g_MAX => 4 -- realistically 400 000   
        )
        port map(
            clk   =>  clk,
            reset =>  reset,
            ce_o  =>  s_en
        );

    --------------------------------------------------------------------
    -- Instance (copy) of cnt_up_down entity performs a 2-bit down
    -- counter
    bin_cnt0 : entity work.cnt_up_down
        generic map(
            g_CNT_WIDTH => 2
        )
        port map(
            clk       => clk,
            reset     => reset,
            en_i      => s_en,
            cnt_up_i  => '0',
            cnt_o     => s_cnt
        );

    --------------------------------------------------------------------
    -- Instance (copy) of hex_7seg entity performs a 7-segment display
    -- decoder
    hex2seg : entity work.hex_7seg
        port map(
            hex_i => s_hex,
            seg_o => seg_o
        );

    --------------------------------------------------------------------
    -- p_mux:
    -- A combinational process that implements a multiplexer for
    -- selecting data for a single digit, a decimal point signal, and 
    -- switches the common anodes of each display.
    --------------------------------------------------------------------
    p_mux : process(s_cnt, data0_i, data1_i, data2_i, data3_i)
    begin
        case s_cnt is
            when "11" =>
                s_hex <= data0_i;
                dig_o <= "0111";

            when "10" =>
                s_hex <= data1_i;
                dig_o <= "1011";

            when "01" =>
                s_hex <= data2_i;
                dig_o <= "1101";

            when others =>
                s_hex <= data3_i;
                dig_o <= "1110";

        end case;
    end process p_mux;

end architecture Behavioral;
``` 

### clock_enable (not simulated seperately, was simulated during computer excersises)

#### Description:

This is a clock divider, similar to what is used in the timer block, it counts up to a predefined (g_MAX) number of clock pulses, and toggles it's output accordingly, to create a slower clock, that drives the other blocks in the display driver. It has a synchronous reset, since the condition for it is only checked after determining a rising edge clock event.

### cnt_up_down (not simulated seperately, was simulated during computer excersises)

#### Description:

A counter used by the multiplexer process to determine which input it is supposed to connect to the output. Since this is a four digit number, it counts from 0 to 3, then wraps around. It's also able to change between counting up and down, thus the name, but we do not use this feature in the project.

### hex7seg (not simulated seperately, was simulated during computer excersises)

#### Description:

This block assigns a value to the output of the multiplexer process, assigning seven-bit output values to the four-bit input ones, controlling each segment. It is set up to control a common anode display (lights up on '0'). A small modification was needed here, since "1111" is used as a value to communicate that nothing is lit up on the display, so its assigned output was changed to "1111111" 

## TOP module description and simulations

### door_lock

#### Visual representation:

doorlockblock

#### Description:

This is the block that houses all interconnecting internal signals for the entire project. It has been made separate from the top block, so that the project's code isn't entirely dependent on the used Arty A7-100T and a potential change of the FPGA board is easier to implement, e.g. top is effectively seperate from the functional code. In the simulation screenshots below we can see the entire project working (simulations are split for value readability). 

In the first one we can see: First, a situation where two buttons are pressed at the same time. We can see it chooses one of them at random, and proceeds as if only one button was pressed, which is the wanted result, as was already mentioned in the keypad_driver section. Then there is the manual reset being tested, we see the that the display wipes itself and the lock returns to the initial neutral state as wanted. The last thing tested is the autoreset, two buttons (wrong combination, doesn't really matter in this case) have been pressed, then, after an idle period with no input, the autoreset signal (internal, not shown, effects observable) is triggered, wiping the display and sending the lock to NEUTRAL, which is the expected result.

In the second one: First, a correct combination is entered ("3142", the default), which changes the locks state from NEUTRAL to PASS0, PASS1, PASS2 and then PASS_FINAL, which opens the relay, lights up the green LED and sends a signal to the timer which starts counting as we can see. When the door is opened, set is pressed and held and a new password is entered ("1234"), rewriting the values stored in the register block (we can see checker inputs connected to these). When the timer reaches five "ticks" it sends the lock to NEUTRAL, turning off the relay, LED and wiping the display and timer. After a while, "1234" is entered, the lock again step by step enters the PASS_FINAL state. Then, when the door is opened, set is held and reset is pressed, the correct combination changes to the default "3142" and immediately without waiting for the timer to finish sets the state to NEUTRAL, except for the display, relay and LED, which wipes/ turns off when reset is released. This could be problematic, since this way, after entering the correct PIN and holding set and reset while the door is opened, it can be held open indefinetly, as long as reset is being held down. A potential problem to be fixed in a future version, but since it requires the knowledge of the password in the first place, it's not that major of an issue. The last thing checked is the ability to enter the same number twice, which we see works, but since the combination is wrong (even though three out of four values are correct, showing that the order of the entered numbers matters), we go through the FAIL states up to FAIL_FINAL, where we see the red LED light up, timer start up, lasting in this state for one "tick" and then returning to NEUTRAL.

Thus, we see the lock fulfills the project goals set at the start, and as far as we have been able to find, has no major issues, although a small number of minor ones are still present at this time (both with the set password feature), mentioned above, namely that the interval for which the password can be changed is fixed (it is desirable to extend it by holding down the set button) and then the fact that after a set+reset password change, holding reset keeps the door open indefinetly.

#### Simulation waveforms:

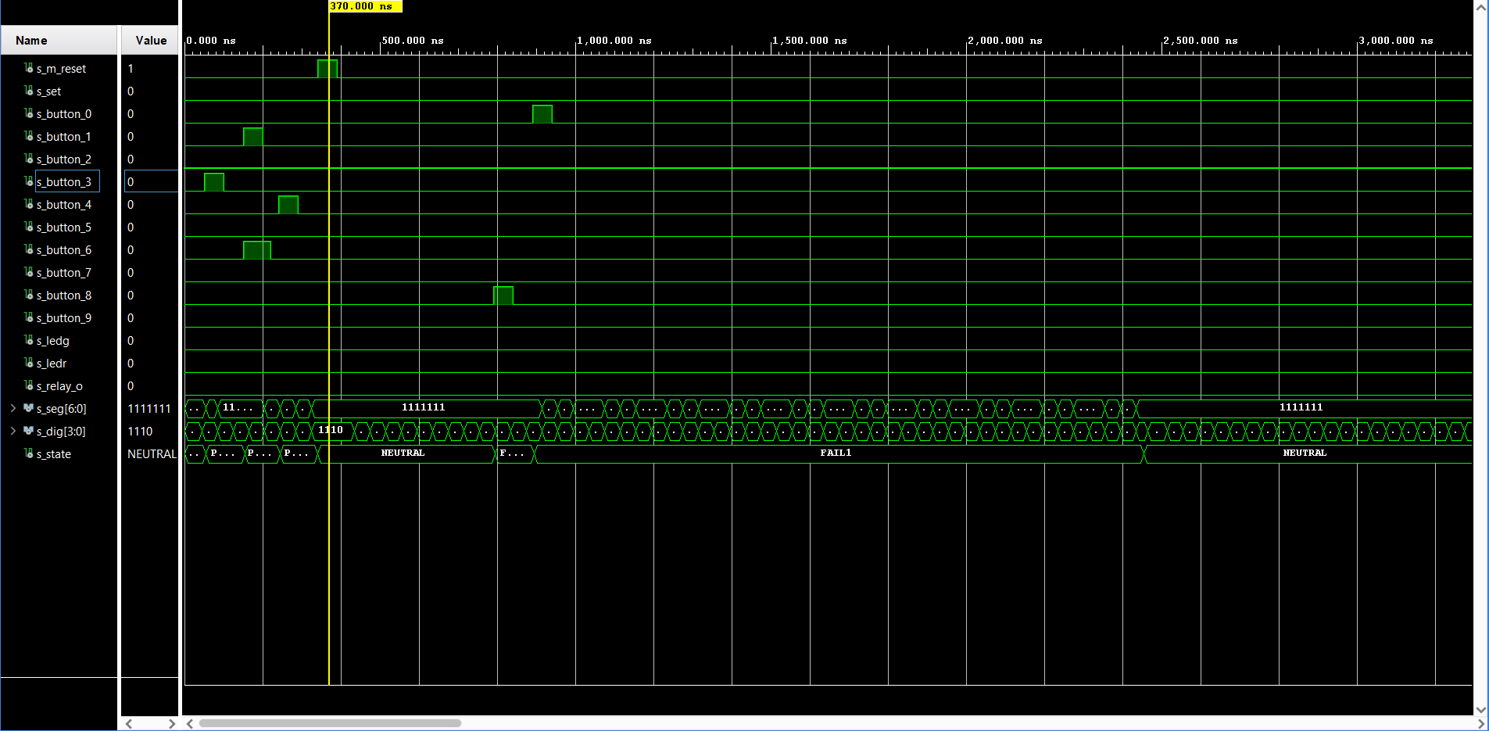
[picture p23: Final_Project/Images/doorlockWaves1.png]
doorlockWaves


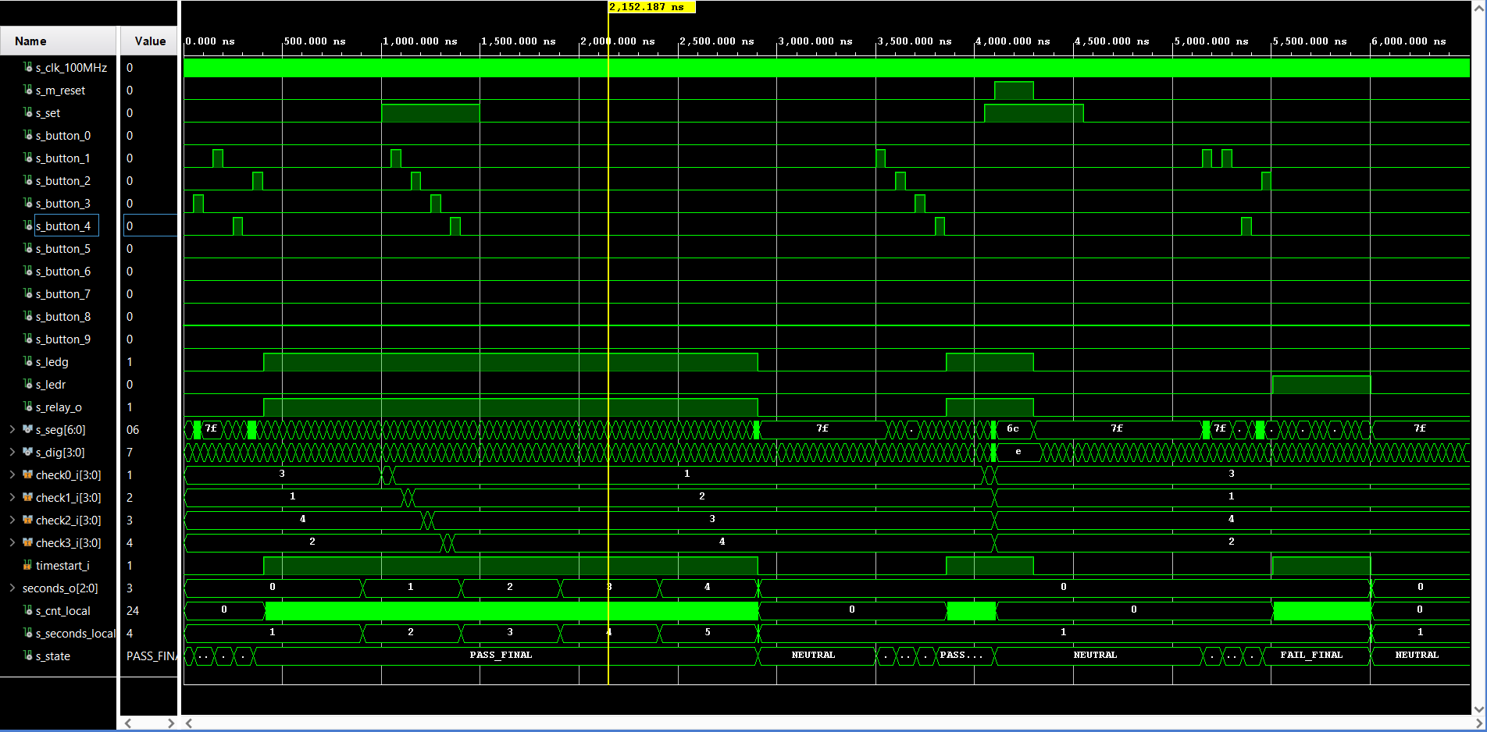
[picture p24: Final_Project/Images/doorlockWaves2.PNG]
doorlockWaves


#### testbench (both in one file): [tb_door_lock.vhd](Final_Project/Testbench/tb_door_lock.vhd)

#### VHDL architecture:
```vhdl
architecture Behavioral of door_lock is

    signal s_num  : STD_LOGIC_VECTOR (4 - 1 downto 0);
    signal s_pos  : STD_LOGIC_VECTOR (2 - 1 downto 0);
    signal s_act  : STD_LOGIC;
    
    signal s_reset_o : STD_LOGIC;
    signal s_a_reset : STD_LOGIC;
    
    signal s_reg0  : STD_LOGIC_VECTOR (4 - 1 downto 0);
    signal s_reg1  : STD_LOGIC_VECTOR (4 - 1 downto 0);
    signal s_reg2  : STD_LOGIC_VECTOR (4 - 1 downto 0);
    signal s_reg3  : STD_LOGIC_VECTOR (4 - 1 downto 0);
    
    signal s_check0  : STD_LOGIC_VECTOR (4 - 1 downto 0);
    signal s_check1  : STD_LOGIC_VECTOR (4 - 1 downto 0);
    signal s_check2  : STD_LOGIC_VECTOR (4 - 1 downto 0);
    signal s_check3  : STD_LOGIC_VECTOR (4 - 1 downto 0);
    
    signal s_driver0  : STD_LOGIC_VECTOR (4 - 1 downto 0);
    signal s_driver1  : STD_LOGIC_VECTOR (4 - 1 downto 0);
    signal s_driver2  : STD_LOGIC_VECTOR (4 - 1 downto 0);
    signal s_driver3  : STD_LOGIC_VECTOR (4 - 1 downto 0);
    
    signal s_relay  : STD_LOGIC;

begin

    keypad_driver0  : entity work.keypad_driver
        port map(
            clk         => clk,  
            reset       => s_reset_o,
        
            button_set  => set,
            button_0    => button_0,
            button_1    => button_1,
            button_2    => button_2,
            button_3    => button_3,
            button_4    => button_4,
            button_5    => button_5,
            button_6    => button_6,
            button_7    => button_7,
            button_8    => button_8,
            button_9    => button_9,
                    
            a_reset_o   => s_a_reset,        
            act_o       => s_act,
            pos_o       => s_pos,
            num_o       => s_num
        );
        
    reset_driver0   : entity work.reset_driver
        port map(
            m_reset     => m_reset,
            a_reset     => s_a_reset,
            
            reset_o     => s_reset_o   
        );
        
    demux0  : entity work.demux
        port map(
            butt_i      => s_num,
            pos_i       => s_pos,
            
            demux0_o    => s_reg0,
            demux1_o    => s_reg1,
            demux2_o    => s_reg2,
            demux3_o    => s_reg3
        );
        
    reg_4_40  : entity work.reg_4_4
        port map(
            set_i       => set,
            pass_i      => s_relay,
            reset_i     => s_reset_o,
            reg0_i      => s_reg0,
            reg1_i      => s_reg1,
            reg2_i      => s_reg2,
            reg3_i      => s_reg3,
            
            reg0_o      => s_check0,
            reg1_o      => s_check1,
            reg2_o      => s_check2,
            reg3_o      => s_check3
        );
        
    checker0  : entity work.checker
        port map(
            clk         => clk,
            butt_i      => s_num,
            reset_i     => s_reset_o,
            write_i     => s_act,
            
            ledg_o      => ledg_o,
            ledr_o      => ledr_o,
            
            relayext_o  => relayext_o,
            relayint_o  => s_relay,
            check0_i    => s_check0,
            check1_i    => s_check1,
            check2_i    => s_check2,
            check3_i    => s_check3,
            
            check0_o    => s_driver0,
            check1_o    => s_driver1,
            check2_o    => s_driver2,
            check3_o    => s_driver3
        );
       
    driver_7seg_4digits0 : entity work.driver_7seg_4digits
        port map(
            clk          => clk,
            reset        => s_reset_o,
            
            data0_i      => s_driver0,
            data1_i      => s_driver1,
            data2_i      => s_driver2,
            data3_i      => s_driver3,
            
            dig_o        => dig_o,
            seg_o        => seg_o
        );

end Behavioral;
``` 

### TOP

#### Visual representation:

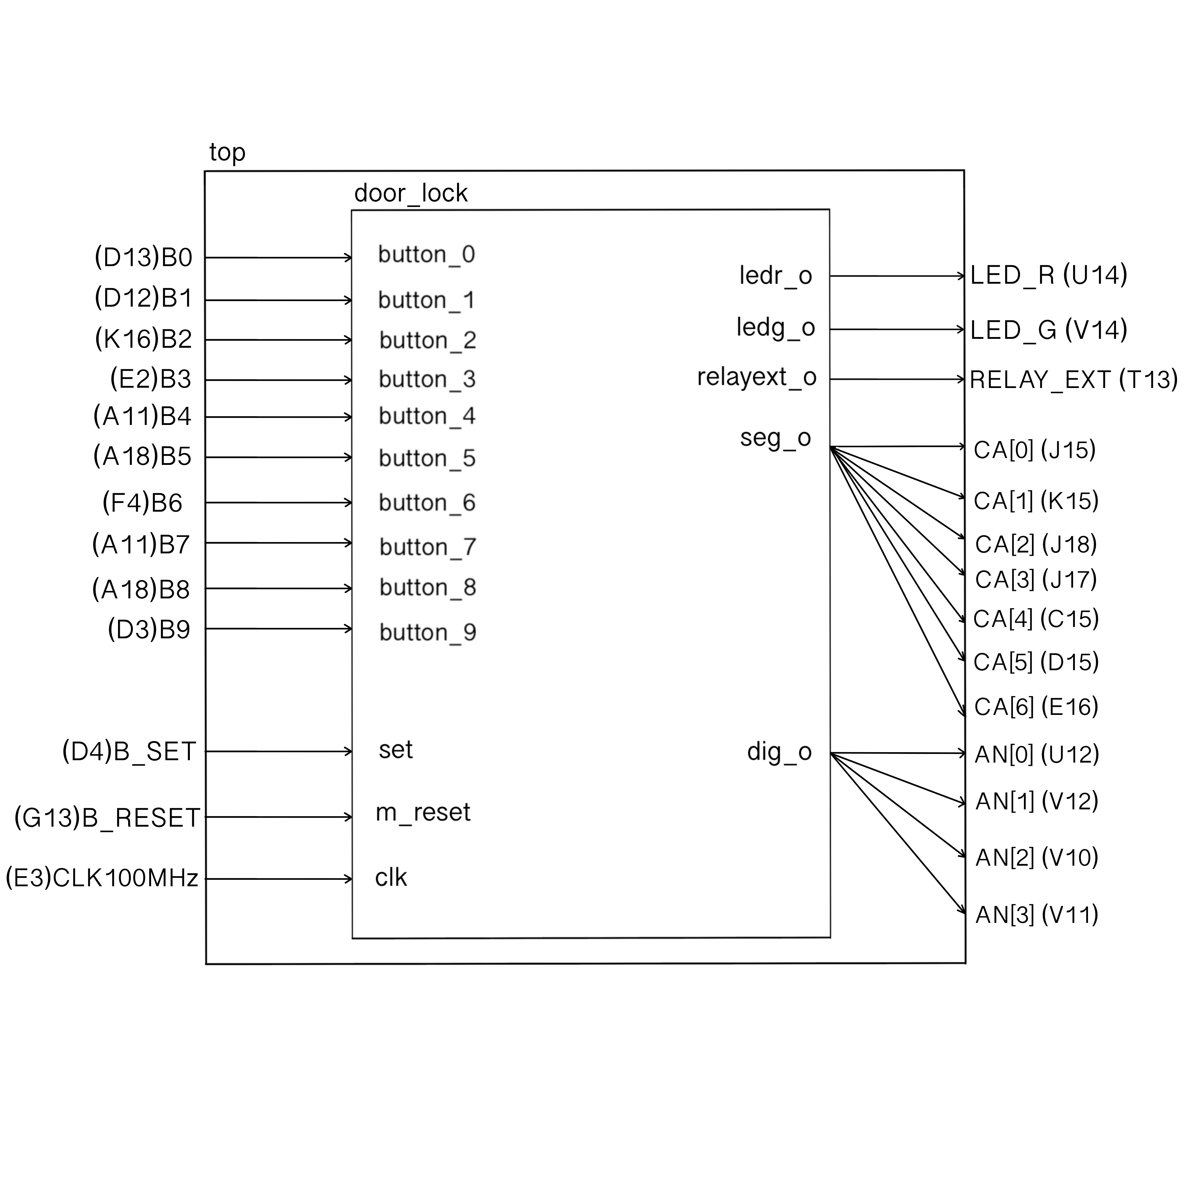
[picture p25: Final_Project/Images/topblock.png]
topblock


#### Description:

Provides interface between the project's (door_lock's) code and the pins of the FPGA. The chosen pins can be seen in the diagram above or the VHDL code below.

#### Constraints: [Arty-A7-100T.xdc](Final_Project/Constraints/Arty-A7-100T.xdc)
#### Bitstream file: [top.bit](Project_Files/Bitstream/top.bit)

#### VHDL architecture:
```vhdl
architecture Behavioral of top is

begin
    door_lock : entity work.door_lock
        port map(
            clk         => CLK100MHZ,
            -------------------------
            button_0    => B0,
            button_1    => B1,
            button_2    => B2,
            button_3    => B3,
            button_4    => B4,
            button_5    => B5,
            button_6    => B6,
            button_7    => B7,
            button_8    => B8,
            button_9    => B9,
            set         => B_SET,
            m_reset     => B_RESET,
            -------------------------
            ledg_o      => LED_G,
            ledr_o      => LED_R,
            relayext_o  => RELAY_EXT,
            seg_o       => CA, 
            dig_o       => AN  
        );

end Behavioral;
```
### Project Files: [door_lock.zip](Project_Files/door_lock.zip)

## Video

[Video na YouTube](https://www.youtube.com/watch?v=wTUz-jFWRrE)

## References

   1. https://github.com/tomas-fryza/Digital-electronics-1
   2. https://www.youtube.com/channel/UCbUe5SLMSZlSzCuJP81lU0A and https://www.youtube.com/c/iit/videos
   3. https://forums.xilinx.com/

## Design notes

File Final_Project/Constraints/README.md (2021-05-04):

```
## This file is a general .xdc for the Arty A7-100 Rev. D
## To use it in a project:
## - uncomment the lines corresponding to used pins
## - rename the used ports (in each line, after get_ports) according to the top level signal names in the project

## Clock signal
set_property -dict { PACKAGE_PIN E3    IOSTANDARD LVCMOS33 } [get_ports { CLK100MHZ }]; #IO_L12P_T1_MRCC_35 Sch=gclk[100]
#create_clock -add -name sys_clk_pin -period 10.00 -waveform {0 5} [get_ports { CLK100MHZ }];

## Switches
#set_property -dict { PACKAGE_PIN A8    IOSTANDARD LVCMOS33 } [get_ports { sw[0] }]; #IO_L12N_T1_MRCC_16 Sch=sw[0]
#set_property -dict { PACKAGE_PIN C11   IOSTANDARD LVCMOS33 } [get_ports { sw[1] }]; #IO_L13P_T2_MRCC_16 Sch=sw[1]
#set_property -dict { PACKAGE_PIN C10   IOSTANDARD LVCMOS33 } [get_ports { sw[2] }]; #IO_L13N_T2_MRCC_16 Sch=sw[2]
#set_property -dict { PACKAGE_PIN A10   IOSTANDARD LVCMOS33 } [get_ports { sw[3] }]; #IO_L14P_T2_SRCC_16 Sch=sw[3]

## RGB LEDs
#set_property -dict { PACKAGE_PIN E1    IOSTANDARD LVCMOS33 } [get_ports { led0_b }]; #IO_L18N_T2_35 Sch=led0_b
#set_property -dict { PACKAGE_PIN F6    IOSTANDARD LVCMOS33 } [get_ports { led0_g }]; #IO_L19N_T3_VREF_35 Sch=led0_g
#set_property -dict { PACKAGE_PIN G6    IOSTANDARD LVCMOS33 } [get_ports { led0_r }]; #IO_L19P_T3_35 Sch=led0_r
#set_property -dict { PACKAGE_PIN G4    IOSTANDARD LVCMOS33 } [get_ports { led1_b }]; #IO_L20P_T3_35 Sch=led1_b
#set_property -dict { PACKAGE_PIN J4    IOSTANDARD LVCMOS33 } [get_ports { led1_g }]; #IO_L21P_T3_DQS_35 Sch=led1_g
#set_property -dict { PACKAGE_PIN G3    IOSTANDARD LVCMOS33 } [get_ports { led1_r }]; #IO_L20N_T3_35 Sch=led1_r
#set_property -dict { PACKAGE_PIN H4    IOSTANDARD LVCMOS33 } [get_ports { led2_b }]; #IO_L21N_T3_DQS_35 Sch=led2_b
#set_property -dict { PACKAGE_PIN J2    IOSTANDARD LVCMOS33 } [get_ports { led2_g }]; #IO_L22N_T3_35 Sch=led2_g
#set_property -dict { PACKAGE_PIN J3    IOSTANDARD LVCMOS33 } [get_ports { led2_r }]; #IO_L22P_T3_35 Sch=led2_r
#set_property -dict { PACKAGE_PIN K2    IOSTANDARD LVCMOS33 } [get_ports { led3_b }]; #IO_L23P_T3_35 Sch=led3_b
#set_property -dict { PACKAGE_PIN H6    IOSTANDARD LVCMOS33 } [get_ports { led3_g }]; #IO_L24P_T3_35 Sch=led3_g
#set_property -dict { PACKAGE_PIN K1    IOSTANDARD LVCMOS33 } [get_ports { led3_r }]; #IO_L23N_T3_35 Sch=led3_r

## LEDs
#set_property -dict { PACKAGE_PIN H5    IOSTANDARD LVCMOS33 } [get_ports { led[0] }]; #IO_L24N_T3_35 Sch=led[4]
#set_property -dict { PACKAGE_PIN J5    IOSTANDARD LVCMOS33 } [get_ports { led[1] }]; #IO_25_35 Sch=led[5]
#set_property -dict { PACKAGE_PIN T9    IOSTANDARD LVCMOS33 } [get_ports { led[2] }]; #IO_L24P_T3_A01_D17_14 Sch=led[6]
#set_property -dict { PACKAGE_PIN T10   IOSTANDARD LVCMOS33 } [get_ports { led[3] }]; #IO_L24N_T3_A00_D16_14 Sch=led[7]

## Buttons
#set_property -dict { PACKAGE_PIN D9    IOSTANDARD LVCMOS33 } [get_ports { btn[0] }]; #IO_L6N_T0_VREF_16 Sch=btn[0]
#set_property -dict { PACKAGE_PIN C9    IOSTANDARD LVCMOS33 } [get_ports { btn[1] }]; #IO_L11P_T1_SRCC_16 Sch=btn[1]
#set_property -dict { PACKAGE_PIN B9    IOSTANDARD LVCMOS33 } [get_ports { btn[2] }]; #IO_L11N_T1_SRCC_16 Sch=btn[2]
#set_property -dict { PACKAGE_PIN B8    IOSTANDARD LVCMOS33 } [get_ports { btn[3] }]; #IO_L12P_T1_MRCC_16 Sch=btn[3]

## Pmod Header JA
set_property -dict { PACKAGE_PIN G13   IOSTANDARD LVCMOS33 } [get_ports { B_SET }]; #IO_0_15 Sch=ja[1]
set_property -dict { PACKAGE_PIN B11   IOSTANDARD LVCMOS33 } [get_ports { B7 }]; #IO_L4P_T0_15 Sch=ja[2]
set_property -dict { PACKAGE_PIN A11   IOSTANDARD LVCMOS33 } [get_ports { B4 }]; #IO_L4N_T0_15 Sch=ja[3]
set_property -dict { PACKAGE_PIN D12   IOSTANDARD LVCMOS33 } [get_ports { B1 }]; #IO_L6P_T0_15 Sch=ja[4]
set_property -dict { PACKAGE_PIN D13   IOSTANDARD LVCMOS33 } [get_ports { B0 }]; #IO_L6N_T0_VREF_15 Sch=ja[7]
set_property -dict { PACKAGE_PIN B18   IOSTANDARD LVCMOS33 } [get_ports { B8 }]; #IO_L10P_T1_AD11P_15 Sch=ja[8]
set_property -dict { PACKAGE_PIN A18   IOSTANDARD LVCMOS33 } [get_ports { B5 }]; #IO_L10N_T1_AD11N_15 Sch=ja[9]
set_property -dict { PACKAGE_PIN K16   IOSTANDARD LVCMOS33 } [get_ports { B2 }]; #IO_25_15 Sch=ja[10]

## Pmod Header JB
#set_property -dict { PACKAGE_PIN E15   IOSTANDARD LVCMOS33 } [get_ports { jb[0] }]; #IO_L11P_T1_SRCC_15 Sch=jb_p[1]
set_property -dict { PACKAGE_PIN E16   IOSTANDARD LVCMOS33 } [get_ports { CA[6] }]; #IO_L11N_T1_SRCC_15 Sch=jb_n[1]
set_property -dict { PACKAGE_PIN D15   IOSTANDARD LVCMOS33 } [get_ports { CA[5] }]; #IO_L12P_T1_MRCC_15 Sch=jb_p[2]
set_property -dict { PACKAGE_PIN C15   IOSTANDARD LVCMOS33 } [get_ports { CA[4] }]; #IO_L12N_T1_MRCC_15 Sch=jb_n[2]
set_property -dict { PACKAGE_PIN J17   IOSTANDARD LVCMOS33 } [get_ports { CA[3] }]; #IO_L23P_T3_FOE_B_15 Sch=jb_p[3]
set_property -dict { PACKAGE_PIN J18   IOSTANDARD LVCMOS33 } [get_ports { CA[2] }]; #IO_L23N_T3_FWE_B_15 Sch=jb_n[3]
set_property -dict { PACKAGE_PIN K15   IOSTANDARD LVCMOS33 } [get_ports { CA[1] }]; #IO_L24P_T3_RS1_15 Sch=jb_p[4]
set_property -dict { PACKAGE_PIN J15   IOSTANDARD LVCMOS33 } [get_ports { CA[0] }]; #IO_L24N_T3_RS0_15 Sch=jb_n[4]

## Pmod Header JC
set_property -dict { PACKAGE_PIN U12   IOSTANDARD LVCMOS33 } [get_ports { AN[0] }]; #IO_L20P_T3_A08_D24_14 Sch=jc_p[1]
set_property -dict { PACKAGE_PIN V12   IOSTANDARD LVCMOS33 } [get_ports { AN[1] }]; #IO_L20N_T3_A07_D23_14 Sch=jc_n[1]
set_property -dict { PACKAGE_PIN V10   IOSTANDARD LVCMOS33 } [get_ports { AN[2] }]; #IO_L21P_T3_DQS_14 Sch=jc_p[2]
set_property -dict { PACKAGE_PIN V11   IOSTANDARD LVCMOS33 } [get_ports { AN[3] }]; #IO_L21N_T3_DQS_A06_D22_14 Sch=jc_n[2]
set_property -dict { PACKAGE_PIN U14   IOSTANDARD LVCMOS33 } [get_ports { LED_R }]; #IO_L22P_T3_A05_D21_14 Sch=jc_p[3]
set_property -dict { PACKAGE_PIN V14   IOSTANDARD LVCMOS33 } [get_ports { LED_G }]; #IO_L22N_T3_A04_D20_14 Sch=jc_n[3]
set_property -dict { PACKAGE_PIN T13   IOSTANDARD LVCMOS33 } [get_ports { RELAY_EXT }]; #IO_L23P_T3_A03_D19_14 Sch=jc_p[4]
#set_property -dict { PACKAGE_PIN U13   IOSTANDARD LVCMOS33 } [get_ports { jc[7] }]; #IO_L23N_T3_A02_D18_14 Sch=jc_n[4]

## Pmod Header JD
set_property -dict { PACKAGE_PIN D4    IOSTANDARD LVCMOS33 } [get_ports { B_RESET }]; #IO_L11N_T1_SRCC_35 Sch=jd[1]
set_property -dict { PACKAGE_PIN D3    IOSTANDARD LVCMOS33 } [get_ports { B9 }]; #IO_L12N_T1_MRCC_35 Sch=jd[2]
set_property -dict { PACKAGE_PIN F4    IOSTANDARD LVCMOS33 } [get_ports { B6 }]; #IO_L13P_T2_MRCC_35 Sch=jd[3]
#set_property -dict { PACKAGE_PIN F3    IOSTANDARD LVCMOS33 } [get_ports { jd[3] }]; #IO_L13N_T2_MRCC_35 Sch=jd[4]
set_property -dict { PACKAGE_PIN E2    IOSTANDARD LVCMOS33 } [get_ports { B3 }]; #IO_L14P_T2_SRCC_35 Sch=jd[7]
#set_property -dict { PACKAGE_PIN D2    IOSTANDARD LVCMOS33 } [get_ports { jd[5] }]; #IO_L14N_T2_SRCC_35 Sch=jd[8]
#set_property -dict { PACKAGE_PIN H2    IOSTANDARD LVCMOS33 } [get_ports { jd[6] }]; #IO_L15P_T2_DQS_35 Sch=jd[9]
#set_property -dict { PACKAGE_PIN G2    IOSTANDARD LVCMOS33 } [get_ports { jd[7] }]; #IO_L15N_T2_DQS_35 Sch=jd[10]

## USB-UART Interface
#set_property -dict { PACKAGE_PIN D10   IOSTANDARD LVCMOS33 } [get_ports { uart_rxd_out }]; #IO_L19N_T3_VREF_16 Sch=uart_rxd_out
#set_property -dict { PACKAGE_PIN A9    IOSTANDARD LVCMOS33 } [get_ports { uart_txd_in }]; #IO_L14N_T2_SRCC_16 Sch=uart_txd_in

## ChipKit Outer Digital Header
#set_property -dict { PACKAGE_PIN V15   IOSTANDARD LVCMOS33 } [get_ports { ck_io0  }]; #IO_L16P_T2_CSI_B_14 Sch=ck_io[0]
#set_property -dict { PACKAGE_PIN U16   IOSTANDARD LVCMOS33 } [get_ports { ck_io1  }]; #IO_L18P_T2_A12_D28_14 Sch=ck_io[1]
#set_property -dict { PACKAGE_PIN P14   IOSTANDARD LVCMOS33 } [get_ports { ck_io2  }]; #IO_L8N_T1_D12_14 Sch=ck_io[2]
#set_property -dict { PACKAGE_PIN T11   IOSTANDARD LVCMOS33 } [get_ports { ck_io3  }]; #IO_L19P_T3_A10_D26_14 Sch=ck_io[3]
#set_property -dict { PACKAGE_PIN R12   IOSTANDARD LVCMOS33 } [get_ports { ck_io4  }]; #IO_L5P_T0_D06_14 Sch=ck_io[4]
#set_property -dict { PACKAGE_PIN T14   IOSTANDARD LVCMOS33 } [get_ports { ck_io5  }]; #IO_L14P_T2_SRCC_14 Sch=ck_io[5]
#set_property -dict { PACKAGE_PIN T15   IOSTANDARD LVCMOS33 } [get_ports { ck_io6  }]; #IO_L14N_T2_SRCC_14 Sch=ck_io[6]
#set_property -dict { PACKAGE_PIN T16   IOSTANDARD LVCMOS33 } [get_ports { ck_io7  }]; #IO_L15N_T2_DQS_DOUT_CSO_B_14 Sch=ck_io[7]
#set_property -dict { PACKAGE_PIN N15   IOSTANDARD LVCMOS33 } [get_ports { ck_io8  }]; #IO_L11P_T1_SRCC_14 Sch=ck_io[8]
#set_property -dict { PACKAGE_PIN M16   IOSTANDARD LVCMOS33 } [get_ports { ck_io9  }]; #IO_L10P_T1_D14_14 Sch=ck_io[9]
#set_property -dict { PACKAGE_PIN V17   IOSTANDARD LVCMOS33 } [get_ports { ck_io10 }]; #IO_L18N_T2_A11_D27_14 Sch=ck_io[10]
#set_property -dict { PACKAGE_PIN U18   IOSTANDARD LVCMOS33 } [get_ports { ck_io11 }]; #IO_L17N_T2_A13_D29_14 Sch=ck_io[11]
#set_property -dict { PACKAGE_PIN R17   IOSTANDARD LVCMOS33 } [get_ports { ck_io12 }]; #IO_L12N_T1_MRCC_14 Sch=ck_io[12]
#set_property -dict { PACKAGE_PIN P17   IOSTANDARD LVCMOS33 } [get_ports { ck_io13 }]; #IO_L12P_T1_MRCC_14 Sch=ck_io[13]

## ChipKit Inner Digital Header
#set_property -dict { PACKAGE_PIN U11   IOSTANDARD LVCMOS33 } [get_ports { ck_io26 }]; #IO_L19N_T3_A09_D25_VREF_14 Sch=ck_io[26]
#set_property -dict { PACKAGE_PIN V16   IOSTANDARD LVCMOS33 } [get_ports { ck_io27 }]; #IO_L16N_T2_A15_D31_14 Sch=ck_io[27]
#set_property -dict { PACKAGE_PIN M13   IOSTANDARD LVCMOS33 } [get_ports { ck_io28 }]; #IO_L6N_T0_D08_VREF_14 Sch=ck_io[28]
#set_property -dict { PACKAGE_PIN R10   IOSTANDARD LVCMOS33 } [get_ports { ck_io29 }]; #IO_25_14 Sch=ck_io[29]
#set_property -dict { PACKAGE_PIN R11   IOSTANDARD LVCMOS33 } [get_ports { ck_io30 }]; #IO_0_14 Sch=ck_io[30]
#set_property -dict { PACKAGE_PIN R13   IOSTANDARD LVCMOS33 } [get_ports { ck_io31 }]; #IO_L5N_T0_D07_14 Sch=ck_io[31]
#set_property -dict { PACKAGE_PIN R15   IOSTANDARD LVCMOS33 } [get_ports { ck_io32 }]; #IO_L13N_T2_MRCC_14 Sch=ck_io[32]
#set_property -dict { PACKAGE_PIN P15   IOSTANDARD LVCMOS33 } [get_ports { ck_io33 }]; #IO_L13P_T2_MRCC_14 Sch=ck_io[33]
#set_property -dict { PACKAGE_PIN R16   IOSTANDARD LVCMOS33 } [get_ports { ck_io34 }]; #IO_L15P_T2_DQS_RDWR_B_14 Sch=ck_io[34]
#set_property -dict { PACKAGE_PIN N16   IOSTANDARD LVCMOS33 } [get_ports { ck_io35 }]; #IO_L11N_T1_SRCC_14 Sch=ck_io[35]
#set_property -dict { PACKAGE_PIN N14   IOSTANDARD LVCMOS33 } [get_ports { ck_io36 }]; #IO_L8P_T1_D11_14 Sch=ck_io[36]
#set_property -dict { PACKAGE_PIN U17   IOSTANDARD LVCMOS33 } [get_ports { ck_io37 }]; #IO_L17P_T2_A14_D30_14 Sch=ck_io[37]
#set_property -dict { PACKAGE_PIN T18   IOSTANDARD LVCMOS33 } [get_ports { ck_io38 }]; #IO_L7N_T1_D10_14 Sch=ck_io[38]
#set_property -dict { PACKAGE_PIN R18   IOSTANDARD LVCMOS33 } [get_ports { ck_io39 }]; #IO_L7P_T1_D09_14 Sch=ck_io[39]
#set_property -dict { PACKAGE_PIN P18   IOSTANDARD LVCMOS33 } [get_ports { ck_io40 }]; #IO_L9N_T1_DQS_D13_14 Sch=ck_io[40]
#set_property -dict { PACKAGE_PIN N17   IOSTANDARD LVCMOS33 } [get_ports { ck_io41 }]; #IO_L9P_T1_DQS_14 Sch=ck_io[41]

## ChipKit Outer Analog Header - as Single-Ended Analog Inputs
## NOTE: These ports can be used as single-ended analog inputs with voltages from 0-3.3V (ChipKit analog pins A0-A5) or as digital I/O.
## WARNING: Do not use both sets of constraints at the same time!
## NOTE: The following constraints should be used with the XADC IP core when using these ports as analog inputs.
#set_property -dict { PACKAGE_PIN C5    IOSTANDARD LVCMOS33 } [get_ports { vaux4_n  }]; #IO_L1N_T0_AD4N_35 	   Sch=ck_an_n[0] ChipKit pin=A0
#set_property -dict { PACKAGE_PIN C6    IOSTANDARD LVCMOS33 } [get_ports { vaux4_p  }]; #IO_L1P_T0_AD4P_35 	   Sch=ck_an_p[0] ChipKit pin=A0
#set_property -dict { PACKAGE_PIN A5    IOSTANDARD LVCMOS33 } [get_ports { vaux5_n  }]; #IO_L3N_T0_DQS_AD5N_35 Sch=ck_an_n[1] ChipKit pin=A1
#set_property -dict { PACKAGE_PIN A6    IOSTANDARD LVCMOS33 } [get_ports { vaux5_p  }]; #IO_L3P_T0_DQS_AD5P_35 Sch=ck_an_p[1] ChipKit pin=A1
#set_property -dict { PACKAGE_PIN B4    IOSTANDARD LVCMOS33 } [get_ports { vaux6_n  }]; #IO_L7N_T1_AD6N_35 	   Sch=ck_an_n[2] ChipKit pin=A2
#set_property -dict { PACKAGE_PIN C4    IOSTANDARD LVCMOS33 } [get_ports { vaux6_p  }]; #IO_L7P_T1_AD6P_35 	   Sch=ck_an_p[2] ChipKit pin=A2
#set_property -dict { PACKAGE_PIN A1    IOSTANDARD LVCMOS33 } [get_ports { vaux7_n  }]; #IO_L9N_T1_DQS_AD7N_35 Sch=ck_an_n[3] ChipKit pin=A3
#set_property -dict { PACKAGE_PIN B1    IOSTANDARD LVCMOS33 } [get_ports { vaux7_p  }]; #IO_L9P_T1_DQS_AD7P_35 Sch=ck_an_p[3] ChipKit pin=A3
#set_property -dict { PACKAGE_PIN B2    IOSTANDARD LVCMOS33 } [get_ports { vaux15_n }]; #IO_L10N_T1_AD15N_35   Sch=ck_an_n[4] ChipKit pin=A4
#set_property -dict { PACKAGE_PIN B3    IOSTANDARD LVCMOS33 } [get_ports { vaux15_p }]; #IO_L10P_T1_AD15P_35   Sch=ck_an_p[4] ChipKit pin=A4
#set_property -dict { PACKAGE_PIN C14   IOSTANDARD LVCMOS33 } [get_ports { vaux0_n  }]; #IO_L1N_T0_AD0N_15 	   Sch=ck_an_n[5] ChipKit pin=A5
#set_property -dict { PACKAGE_PIN D14   IOSTANDARD LVCMOS33 } [get_ports { vaux0_p  }]; #IO_L1P_T0_AD0P_15 	   Sch=ck_an_p[5] ChipKit pin=A5
## ChipKit Outer Analog Header - as Digital I/O
## NOTE: The following constraints should be used when using these ports as digital I/O.
#set_property -dict { PACKAGE_PIN F5    IOSTANDARD LVCMOS33 } [get_ports { ck_a0 }]; #IO_0_35 Sch=ck_a[0]
#set_property -dict { PACKAGE_PIN D8    IOSTANDARD LVCMOS33 } [get_ports { ck_a1 }]; #IO_L4P_T0_35 Sch=ck_a[1]
#set_property -dict { PACKAGE_PIN C7    IOSTANDARD LVCMOS33 } [get_ports { ck_a2 }]; #IO_L4N_T0_35 Sch=ck_a[2]
#set_property -dict { PACKAGE_PIN E7    IOSTANDARD LVCMOS33 } [get_ports { ck_a3 }]; #IO_L6P_T0_35 Sch=ck_a[3]
#set_property -dict { PACKAGE_PIN D7    IOSTANDARD LVCMOS33 } [get_ports { ck_a4 }]; #IO_L6N_T0_VREF_35 Sch=ck_a[4]
#set_property -dict { PACKAGE_PIN D5    IOSTANDARD LVCMOS33 } [get_ports { ck_a5 }]; #IO_L11P_T1_SRCC_35 Sch=ck_a[5]

## ChipKit Inner Analog Header - as Differential Analog Inputs
## NOTE: These ports can be used as differential analog inputs with voltages from 0-1.0V (ChipKit analog pins A6-A11) or as digital I/O.
## WARNING: Do not use both sets of constraints at the same time!
## NOTE: The following constraints should be used with the XADC core when using these ports as analog inputs.
#set_property -dict { PACKAGE_PIN B7    IOSTANDARD LVCMOS33 } [get_ports { vaux12_p }]; #IO_L2P_T0_AD12P_35 Sch=ad_p[12] ChipKit pin=A6
#set_property -dict { PACKAGE_PIN B6    IOSTANDARD LVCMOS33 } [get_ports { vaux12_n }]; #IO_L2N_T0_AD12N_35 Sch=ad_n[12] ChipKit pin=A7
#set_property -dict { PACKAGE_PIN E6    IOSTANDARD LVCMOS33 } [get_ports { vaux13_p }]; #IO_L5P_T0_AD13P_35 Sch=ad_p[13] ChipKit pin=A8
#set_property -dict { PACKAGE_PIN E5    IOSTANDARD LVCMOS33 } [get_ports { vaux13_n }]; #IO_L5N_T0_AD13N_35 Sch=ad_n[13] ChipKit pin=A9
#set_property -dict { PACKAGE_PIN A4    IOSTANDARD LVCMOS33 } [get_ports { vaux14_p }]; #IO_L8P_T1_AD14P_35 Sch=ad_p[14] ChipKit pin=A10
#set_property -dict { PACKAGE_PIN A3    IOSTANDARD LVCMOS33 } [get_ports { vaux14_n }]; #IO_L8N_T1_AD14N_35 Sch=ad_n[14] ChipKit pin=A11
## ChipKit Inner Analog Header - as Digital I/O
## NOTE: The following constraints should be used when using the inner analog header ports as digital I/O.
#set_property -dict { PACKAGE_PIN B7    IOSTANDARD LVCMOS33 } [get_ports { ck_a6  }]; #IO_L2P_T0_AD12P_35 Sch=ad_p[12]
#set_property -dict { PACKAGE_PIN B6    IOSTANDARD LVCMOS33 } [get_ports { ck_a7  }]; #IO_L2N_T0_AD12N_35 Sch=ad_n[12]
#set_property -dict { PACKAGE_PIN E6    IOSTANDARD LVCMOS33 } [get_ports { ck_a8  }]; #IO_L5P_T0_AD13P_35 Sch=ad_p[13]
#set_property -dict { PACKAGE_PIN E5    IOSTANDARD LVCMOS33 } [get_ports { ck_a9  }]; #IO_L5N_T0_AD13N_35 Sch=ad_n[13]
#set_property -dict { PACKAGE_PIN A4    IOSTANDARD LVCMOS33 } [get_ports { ck_a10 }]; #IO_L8P_T1_AD14P_35 Sch=ad_p[14]
#set_property -dict { PACKAGE_PIN A3    IOSTANDARD LVCMOS33 } [get_ports { ck_a11 }]; #IO_L8N_T1_AD14N_35 Sch=ad_n[14]

## ChipKit SPI
#set_property -dict { PACKAGE_PIN G1    IOSTANDARD LVCMOS33 } [get_ports { ck_miso }]; #IO_L17N_T2_35 Sch=ck_miso
#set_property -dict { PACKAGE_PIN H1    IOSTANDARD LVCMOS33 } [get_ports { ck_mosi }]; #IO_L17P_T2_35 Sch=ck_mosi
#set_property -dict { PACKAGE_PIN F1    IOSTANDARD LVCMOS33 } [get_ports { ck_sck }]; #IO_L18P_T2_35 Sch=ck_sck
#set_property -dict { PACKAGE_PIN C1    IOSTANDARD LVCMOS33 } [get_ports { ck_ss }]; #IO_L16N_T2_35 Sch=ck_ss

## ChipKit I2C
#set_property -dict { PACKAGE_PIN L18   IOSTANDARD LVCMOS33 } [get_ports { ck_scl }]; #IO_L4P_T0_D04_14 Sch=ck_scl
#set_property -dict { PACKAGE_PIN M18   IOSTANDARD LVCMOS33 } [get_ports { ck_sda }]; #IO_L4N_T0_D05_14 Sch=ck_sda
#set_property -dict { PACKAGE_PIN A14   IOSTANDARD LVCMOS33 } [get_ports { scl_pup }]; #IO_L9N_T1_DQS_AD3N_15 Sch=scl_pup
#set_property -dict { PACKAGE_PIN A13   IOSTANDARD LVCMOS33 } [get_ports { sda_pup }]; #IO_L9P_T1_DQS_AD3P_15 Sch=sda_pup

## Misc. ChipKit Ports
#set_property -dict { PACKAGE_PIN M17   IOSTANDARD LVCMOS33 } [get_ports { ck_ioa }]; #IO_L10N_T1_D15_14 Sch=ck_ioa
#set_property -dict { PACKAGE_PIN C2    IOSTANDARD LVCMOS33 } [get_ports { ck_rst }]; #IO_L16P_T2_35 Sch=ck_rst

## SMSC Ethernet PHY
#set_property -dict { PACKAGE_PIN D17   IOSTANDARD LVCMOS33 } [get_ports { eth_col }]; #IO_L16N_T2_A27_15 Sch=eth_col
#set_property -dict { PACKAGE_PIN G14   IOSTANDARD LVCMOS33 } [get_ports { eth_crs }]; #IO_L15N_T2_DQS_ADV_B_15 Sch=eth_crs
#set_property -dict { PACKAGE_PIN F16   IOSTANDARD LVCMOS33 } [get_ports { eth_mdc }]; #IO_L14N_T2_SRCC_15 Sch=eth_mdc
#set_property -dict { PACKAGE_PIN K13   IOSTANDARD LVCMOS33 } [get_ports { eth_mdio }]; #IO_L17P_T2_A26_15 Sch=eth_mdio
#set_property -dict { PACKAGE_PIN G18   IOSTANDARD LVCMOS33 } [get_ports { eth_ref_clk }]; #IO_L22P_T3_A17_15 Sch=eth_ref_clk
#set_property -dict { PACKAGE_PIN C16   IOSTANDARD LVCMOS33 } [get_ports { eth_rstn }]; #IO_L20P_T3_A20_15 Sch=eth_rstn
#set_property -dict { PACKAGE_PIN F15   IOSTANDARD LVCMOS33 } [get_ports { eth_rx_clk }]; #IO_L14P_T2_SRCC_15 Sch=eth_rx_clk
#set_property -dict { PACKAGE_PIN G16   IOSTANDARD LVCMOS33 } [get_ports { eth_rx_dv }]; #IO_L13N_T2_MRCC_15 Sch=eth_rx_dv
#set_property -dict { PACKAGE_PIN D18   IOSTANDARD LVCMOS33 } [get_ports { eth_rxd[0] }]; #IO_L21N_T3_DQS_A18_15 Sch=eth_rxd[0]
#set_property -dict { PACKAGE_PIN E17   IOSTANDARD LVCMOS33 } [get_ports { eth_rxd[1] }]; #IO_L16P_T2_A28_15 Sch=eth_rxd[1]
#set_property -dict { PACKAGE_PIN E18   IOSTANDARD LVCMOS33 } [get_ports { eth_rxd[2] }]; #IO_L21P_T3_DQS_15 Sch=eth_rxd[2]
#set_property -dict { PACKAGE_PIN G17   IOSTANDARD LVCMOS33 } [get_ports { eth_rxd[3] }]; #IO_L18N_T2_A23_15 Sch=eth_rxd[3]
#set_property -dict { PACKAGE_PIN C17   IOSTANDARD LVCMOS33 } [get_ports { eth_rxerr }]; #IO_L20N_T3_A19_15 Sch=eth_rxerr
#set_property -dict { PACKAGE_PIN H16   IOSTANDARD LVCMOS33 } [get_ports { eth_tx_clk }]; #IO_L13P_T2_MRCC_15 Sch=eth_tx_clk
#set_property -dict { PACKAGE_PIN H15   IOSTANDARD LVCMOS33 } [get_ports { eth_tx_en }]; #IO_L19N_T3_A21_VREF_15 Sch=eth_tx_en
#set_property -dict { PACKAGE_PIN H14   IOSTANDARD LVCMOS33 } [get_ports { eth_txd[0] }]; #IO_L15P_T2_DQS_15 Sch=eth_txd[0]
#set_property -dict { PACKAGE_PIN J14   IOSTANDARD LVCMOS33 } [get_ports { eth_txd[1] }]; #IO_L19P_T3_A22_15 Sch=eth_txd[1]
#set_property -dict { PACKAGE_PIN J13   IOSTANDARD LVCMOS33 } [get_ports { eth_txd[2] }]; #IO_L17N_T2_A25_15 Sch=eth_txd[2]
#set_property -dict { PACKAGE_PIN H17   IOSTANDARD LVCMOS33 } [get_ports { eth_txd[3] }]; #IO_L18P_T2_A24_15 Sch=eth_txd[3]

## Quad SPI Flash
#set_property -dict { PACKAGE_PIN L13   IOSTANDARD LVCMOS33 } [get_ports { qspi_cs }]; #IO_L6P_T0_FCS_B_14 Sch=qspi_cs
#set_property -dict { PACKAGE_PIN K17   IOSTANDARD LVCMOS33 } [get_ports { qspi_dq[0] }]; #IO_L1P_T0_D00_MOSI_14 Sch=qspi_dq[0]
#set_property -dict { PACKAGE_PIN K18   IOSTANDARD LVCMOS33 } [get_ports { qspi_dq[1] }]; #IO_L1N_T0_D01_DIN_14 Sch=qspi_dq[1]
#set_property -dict { PACKAGE_PIN L14   IOSTANDARD LVCMOS33 } [get_ports { qspi_dq[2] }]; #IO_L2P_T0_D02_14 Sch=qspi_dq[2]
#set_property -dict { PACKAGE_PIN M14   IOSTANDARD LVCMOS33 } [get_ports { qspi_dq[3] }]; #IO_L2N_T0_D03_14 Sch=qspi_dq[3]

## Power Measurements 
#set_property -dict { PACKAGE_PIN B17   IOSTANDARD LVCMOS33     } [get_ports { vsnsvu_n }]; #IO_L7N_T1_AD2N_15 Sch=ad_n[2]
#set_property -dict { PACKAGE_PIN B16   IOSTANDARD LVCMOS33     } [get_ports { vsnsvu_p }]; #IO_L7P_T1_AD2P_15 Sch=ad_p[2]
#set_property -dict { PACKAGE_PIN B12   IOSTANDARD LVCMOS33     } [get_ports { vsns5v0_n }]; #IO_L3N_T0_DQS_AD1N_15 Sch=ad_n[1]
#set_property -dict { PACKAGE_PIN C12   IOSTANDARD LVCMOS33     } [get_ports { vsns5v0_p }]; #IO_L3P_T0_DQS_AD1P_15 Sch=ad_p[1]
#set_property -dict { PACKAGE_PIN F14   IOSTANDARD LVCMOS33     } [get_ports { isns5v0_n }]; #IO_L5N_T0_AD9N_15 Sch=ad_n[9]
#set_property -dict { PACKAGE_PIN F13   IOSTANDARD LVCMOS33     } [get_ports { isns5v0_p }]; #IO_L5P_T0_AD9P_15 Sch=ad_p[9]
#set_property -dict { PACKAGE_PIN A16   IOSTANDARD LVCMOS33     } [get_ports { isns0v95_n }]; #IO_L8N_T1_AD10N_15 Sch=ad_n[10]
#set_property -dict { PACKAGE_PIN A15   IOSTANDARD LVCMOS33     } [get_ports { isns0v95_p }]; #IO_L8P_T1_AD10P_15 Sch=ad_p[10]
```

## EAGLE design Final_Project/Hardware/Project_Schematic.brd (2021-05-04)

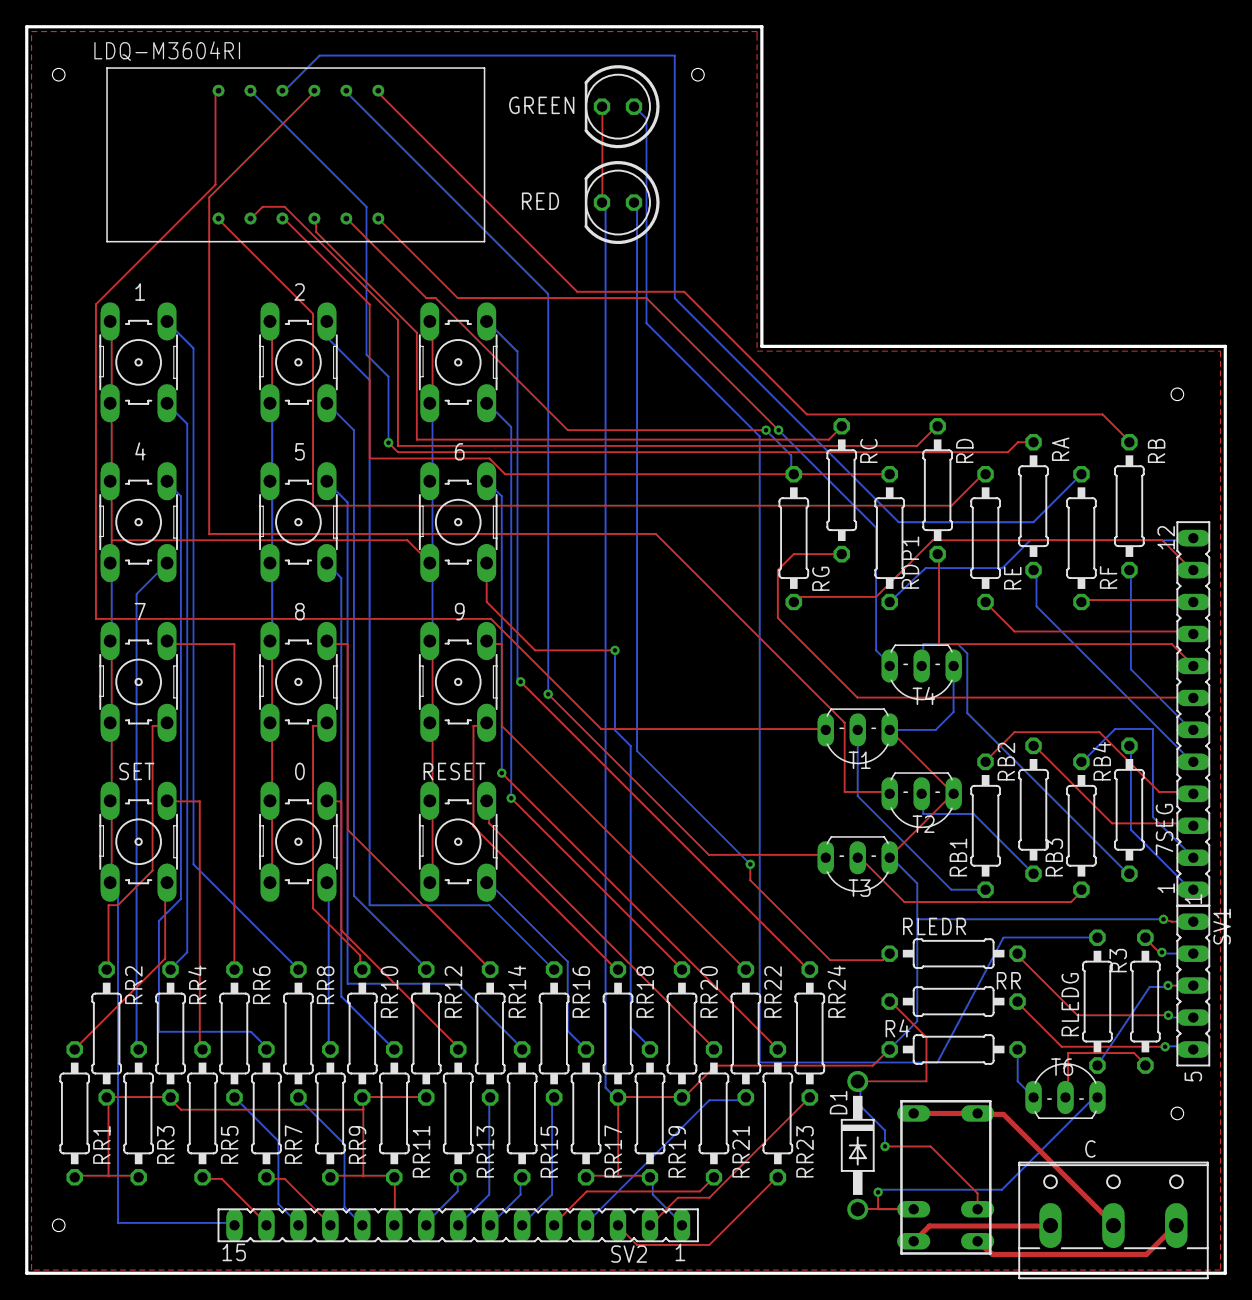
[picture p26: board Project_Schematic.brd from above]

Board: 2 copper layers, 95.2 x 99.1 mm, 67 parts (0 on the bottom side), 77 nets.

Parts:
0, 1, 2, 3, 4, 5, 6, 7, 8, 9: B3F-10XX
7SEG: FE12
C: W237-103
D1: 1N4004; DO41-10
GREEN: LED5MM
K2: G5V1
LDQ-M3604RI: 4X7SEGMENTDISPLAY.; 4X7SCHEM
R3: 12k; 0207/10
R4: 10; 0207/10
RA: 47; 0207/10
RB: 47; 0207/10
RB1, RB2, RB3, RB4: 3k9; 0207/10
RC: 47; 0207/10
RD: 47; 0207/10
RDP1: 47; 0207/10
RE: 47; 0207/10
RED: LED5MM
RESET: B3F-10XX
RF: 47; 0207/10
RG: 47; 0207/10
RLEDG: 68; 0207/10
RLEDR: 82; 0207/10
RR: 10; 0207/10
RR1, RR2, RR3, RR4, RR9, RR10, RR11, RR12, RR17, RR18, RR19, RR20: 10k; 0207/10
RR5, RR6, RR7, RR8, RR13, RR14, RR15, RR16, RR21, RR22, RR23, RR24: 22; 0207/10
SET: B3F-10XX
SV1: FE05-1
SV2: FE15
T1, T2, T3, T4: 2N3906; TO92-EBC
T6: 2N3903; TO92-EBC

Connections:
A11-7: RR7.2, SV2.12
A18-8: RR15.2, SV2.7
B18-5: RR14.2, SV2.8
C15-E: 7SEG.9, RE.2
D3-6: RR22.2, SV2.4
D4-3: RR21.2, SV2.5
D12-SET: RR8.2, SV2.11
D13-2: RR13.2, SV2.9
D15-F: 7SEG.10, RF.2
E2-RESET: RR24.2, SV2.2
E15-DP1: 7SEG.12, RDP1.1
E16-G: 7SEG.11, RG.2
F4-9: RR23.2, SV2.3
GND: GREEN.K, R4.2, RED.K, RR17.2, RR18.2, RR19.2, RR20.2, SV1.1, SV2.1, T1.E, T2.E, T3.E, T4.E
J15-A: 7SEG.5, RA.2
J17-D: 7SEG.8, RD.2
K15-B: 7SEG.6, RB.2
K16-0: RR16.2, SV2.6
unnamed: RB1.1, T1.B
unnamed: LDQ-M3604RI.DIG2, T2.C
unnamed: LDQ-M3604RI.DIG1, T1.C
unnamed: LDQ-M3604RI.DIG3, T3.C
unnamed: LDQ-M3604RI.DIG4, T4.C
unnamed: RB2.1, T2.B
unnamed: RB3.1, T3.B
unnamed: RB4.1, T4.B
unnamed: RR1.2, RR2.2, RR3.2, RR4.2, RR9.2, RR10.2, RR11.2, RR12.2, SV2.10
unnamed: LDQ-M3604RI.A, RA.1
unnamed: LDQ-M3604RI.B, RB.1
unnamed: LDQ-M3604RI.C, RC.1
unnamed: LDQ-M3604RI.D, RD.1
unnamed: LDQ-M3604RI.E, RE.1
unnamed: LDQ-M3604RI.F, RF.1
unnamed: LDQ-M3604RI.G, RG.1
unnamed: LDQ-M3604RI.DP1, RDP1.2
unnamed: RR5.1, SET.1
unnamed: 7.1, RR6.1
unnamed: RR5.2, SV2.14
unnamed: 1.1, RR8.1
unnamed: D1.C, K2.2, RR.2
unnamed: 0.1, RR13.1
unnamed: 8.1, RR14.1
unnamed: 2.1, RR16.1
unnamed: 8.2, RR10.1
unnamed: 5.2, RR11.1
unnamed: R3.1, T6.B
unnamed: R4.1, T6.E
unnamed: 2.2, RR12.1
unnamed: 0.2, RR9.1
unnamed: 5.1, RR15.1
unnamed: GREEN.A, RLEDG.2
unnamed: RED.A, RLEDR.1
unnamed: RR1.1, SET.2
unnamed: 7.2, RR2.1
unnamed: 4.2, RR3.1
unnamed: 1.2, RR4.1
unnamed: 4.1, RR7.1
unnamed: K2.9, T6.C
unnamed: RR6.2, SV2.13
unnamed: 0.3, 0.4, 2.3, 2.4, 5.3, 5.4, 8.3, 8.4
unnamed: RESET.1, RR21.1
unnamed: 9.1, RR22.1
unnamed: 3.1, RR24.1
unnamed: 9.2, RR18.1
unnamed: 6.2, RR19.1
unnamed: 3.2, RR20.1
unnamed: RESET.2, RR17.1
unnamed: 6.1, RR23.1
unnamed: 1.3, 1.4, 3.3, 3.4, 4.3, 4.4, 6.3, 6.4, 7.3, 7.4, 9.3, 9.4, RESET.3, RESET.4, SET.3, SET.4, SV2.15
T13-RELAY: R3.2, SV1.2
U12-DIG1: 7SEG.4, RB1.2
U14-LEDR: RLEDR.2, SV1.4
V10-DIG3: 7SEG.2, RB3.2
V11-DIG4: 7SEG.1, RB4.2
V12-DIG2: 7SEG.3, RB2.2
V14-LEDG: RLEDG.1, SV1.3
VCC: RR.1, SV1.5
